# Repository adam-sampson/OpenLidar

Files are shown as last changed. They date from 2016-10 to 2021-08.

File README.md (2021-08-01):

# OpenLidar
Open Lidar

The idea of this project is to use cheap laser distance modules to create 3D scans of the room. This can be done by rotating the laser distance module on 2 axis with the sensor centered on the junction of those two axis (aka: the sensor is on the center of rotation so it's always at the origin). The main goals of this project are to improve the means that cavers use to survey and map caves as citizen scientists, or to create point-clouds for your own purpose.

The project is developed in 3 parts. 1) The hardware for the gimbal. 2) The software to operate the gimbal. 3) Bluetooth/Serial interface for controlling the device with inputs. 

This is a work in progress and has been submitted to the Hackaday Prize. https://hackaday.io/project/11598-open-lidar

The original project had both hardware and software issues and was scrapped for the newer version located here. For older information you will need to checkout previous commits of this git repository. Issues included: not enough ram on the arduino mini pro to fill an SD card write block (extra SD writes = slow), hardware design of the body created too much friction for fast motor operation, hardware was unstable/wobbly, power supply was exceedingly large to fit in case, hardware was not enclosed in protective enclosure, the yaw motor could turn freely (and be knocked out of position easily), the SF-30B module had excessive noise per reading, etc.

The change in case hardware, microchip used, lidar sensor, and yaw motor assembly all necessitated a full rework of the project here.

The current state of the hardware:
- Yaw axis has been completely redesigned to use 30mm shaft through bearing for greater stability
- Pitch axis has been completely redesigned to use "fieldgoal" design to reduce friction and complexity of shaft
- Case parts have been modeled in Fusion 360 but need to finish printing/testing
- Re-selected new hardware to make use of S42B stepper drivers for simplicity and servo-like capabilities

The current status of the software is that it is capable of:
- Capturing data from LidarLitev3 using enhanced library for speeds of up to 2000/s (with ideal I2C conditions)
- Controlling 2 stepper motors 
- Receiving commands and outputing results over serial
- Write to SD card

Future items needed
- Scan Mode to prevent scanRoom from over-sampling near polar regions
- Add ability to read/write settings to ROM
- Add ability to change default settings
- Create progress indicators and time estimates
- Add ability to save as E57 point cloud file
- Add ability to save as xyz point cloud file
- Add routine for identifying 0 degrees
- Add ability to create custom filename (i.e. date and time)

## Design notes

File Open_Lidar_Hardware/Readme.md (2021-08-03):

# Open Lidar Hardware

This section contains the hardware files for the Open Lidar project.

Fusion 360 files are provided as .f3d files. 

Print ready files are provided as .stl files. 

# 3D Printed Case

- LidarLite mount (printed and fitted)
- Gimbal Mount
  - Fieldgoal (printed and fitted)
  - Shaft left/right to act as yaw shaft and mount to field goal (adjusted for better fit)
  - Shaft gear
  - Yaw Motor Gear
  - Slip Ring Connector
  - Body Top
  - Body Middle
  - Body Base
  - Bearing Retention ring

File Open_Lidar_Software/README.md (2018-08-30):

# OpenLidar
Open Lidar

The idea of this project is to use cheap laser distance modules to create 3D scans of the room. This can be done by rotating the laser distance module on 2 axis with the sensor centered on the junction of those two axis (aka: the sensor is on the center of rotation so it's always at the origin). The main goals of this project are to improve the means that cavers use to survey and map caves as citizen scientists, or to create point-clouds for your own purpose.

The current status of the software is that it is capable of:
- Controlling 2 stepper motors (upgraded since last model)
- Receiving commands and outputing results over serial
- Receiving a few commands from a computer/phone over bluetooth
- Creating a unique file name on the SD card

Bluetooth commands:
- cancel;
- pitch turn <float>;
- pitch rpm <int>;
- pitch microstep <int>;
- pitch enable;
- pitch disable;
- yaw turn <float>;
- yaw rpm <int>;
- yaw microstep <int>;
- yaw enable;
- yaw disable;
- yaw max <int>;
- lidar dist;
- lidar scan;
- lidar test;
- bluetooth; (not used yet)
- sd test <string>;
- motor enable;
- motor disable;

Future items needed
- Interfacing over bluetooth
- Reading data from the Lidar Lite V3 module
- Writing to a microSD card
- Create a new scan room function
- Add filter to prevent scanRoom from over-sampling near polar regions
- Add ability to read/write settings to ROM
- Add ability to change default settings
- Create progress indicators and time estimates
- Add ability to save as E57 point cloud file
- Add routine for identifying 0 degrees
- Add ability to create custom filename (i.e. date and time)

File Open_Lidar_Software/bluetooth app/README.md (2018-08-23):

# Bluetooth App

The attached zip file contains an app from http://www.jnhuamao.cn/index_en.asp?ID=1 that allows for connecting to an HM-10 device in windows 10 64 bit. 

This app is required because the BLE device does not get it's own port assigned to it as other non-BLE modules do. 

To install the app follow the instructions in the README inside the zip file. Then find it in your program files just like any other app.

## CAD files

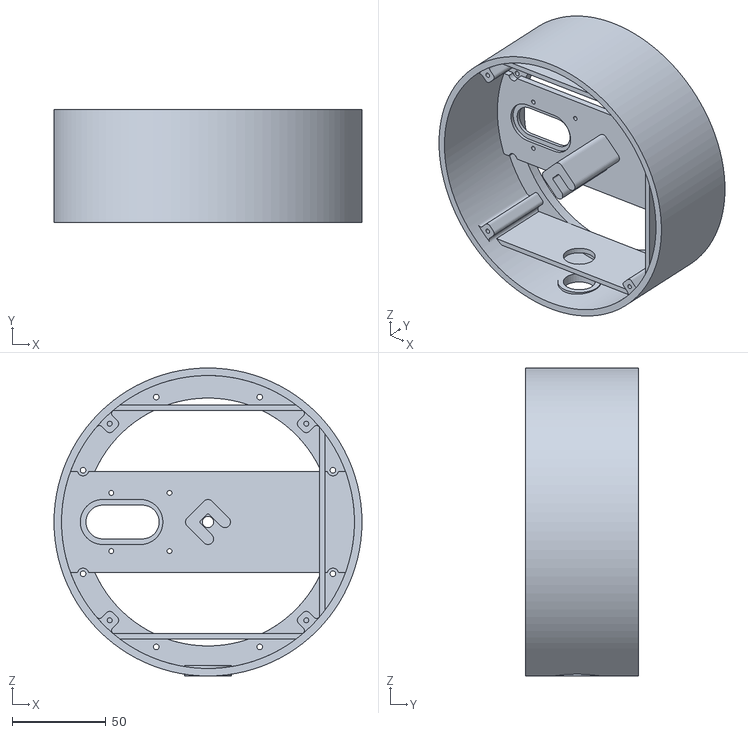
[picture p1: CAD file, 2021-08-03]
Open_Lidar_Hardware/stl/GimbalBaseMiddle.stl
164.0 x 60.0 x 164.0

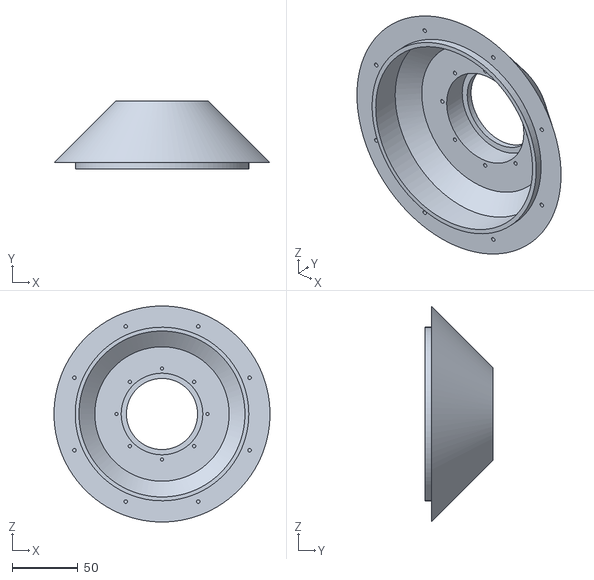
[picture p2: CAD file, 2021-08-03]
Open_Lidar_Hardware/stl/GimbalBaseTop.stl
164.0 x 52.0 x 164.0

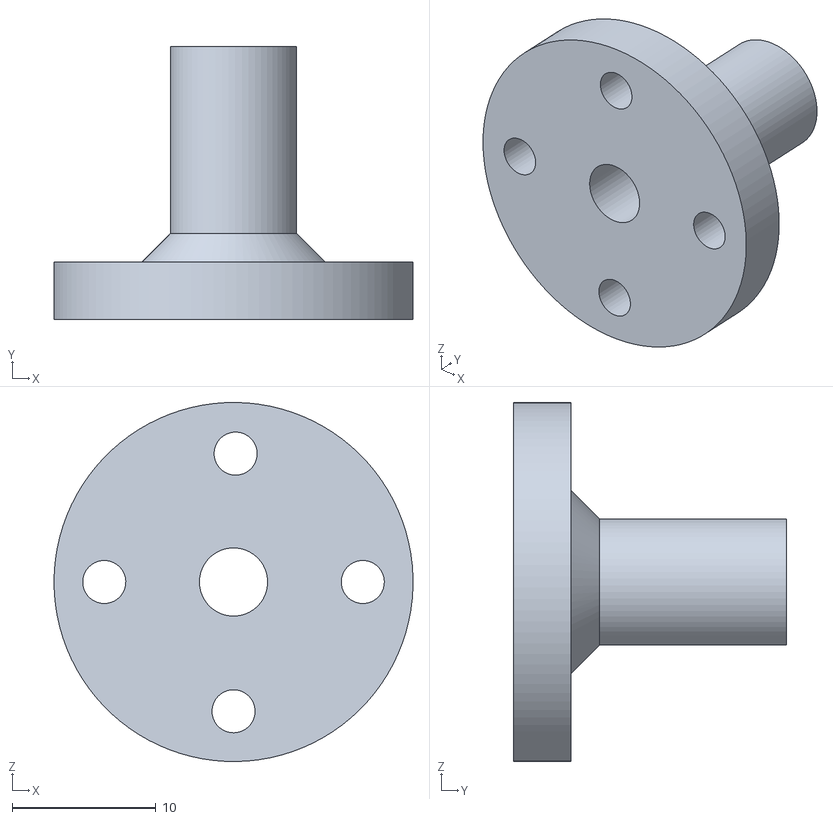
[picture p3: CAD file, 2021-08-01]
Open_Lidar_Hardware/stl/GimbalSlipRingConnector.stl
25.0 x 19.0 x 25.0

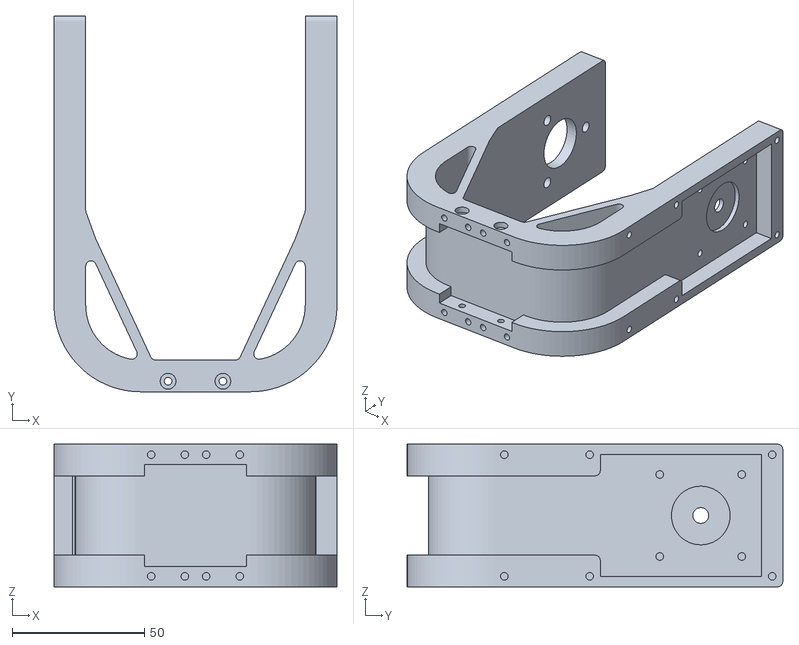
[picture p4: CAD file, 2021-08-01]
Open_Lidar_Hardware/stl/GimalFieldgoal.stl
107.0 x 142.0 x 54.0

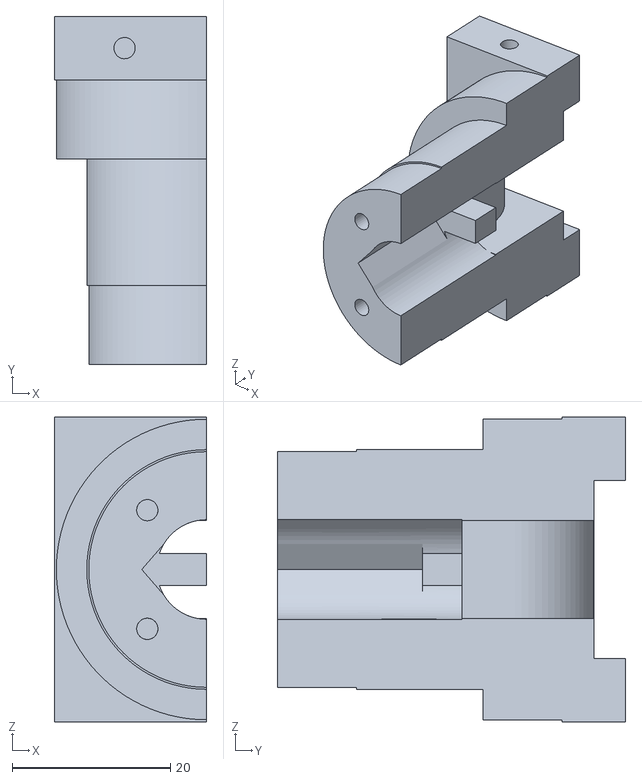
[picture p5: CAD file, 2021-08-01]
Open_Lidar_Hardware/stl/GimbalShaftLeft.stl
19.3 x 44.0 x 38.5

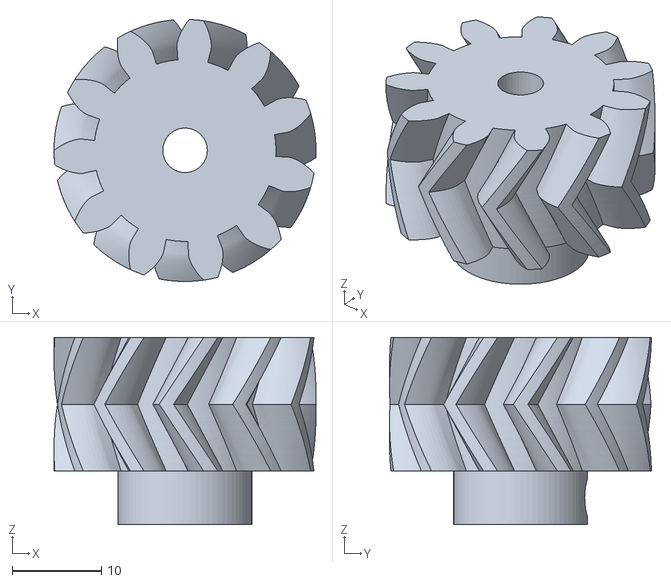
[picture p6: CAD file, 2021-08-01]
Open_Lidar_Hardware/stl/GimbalYawMotorGear.stl
29.4 x 29.4 x 21.0

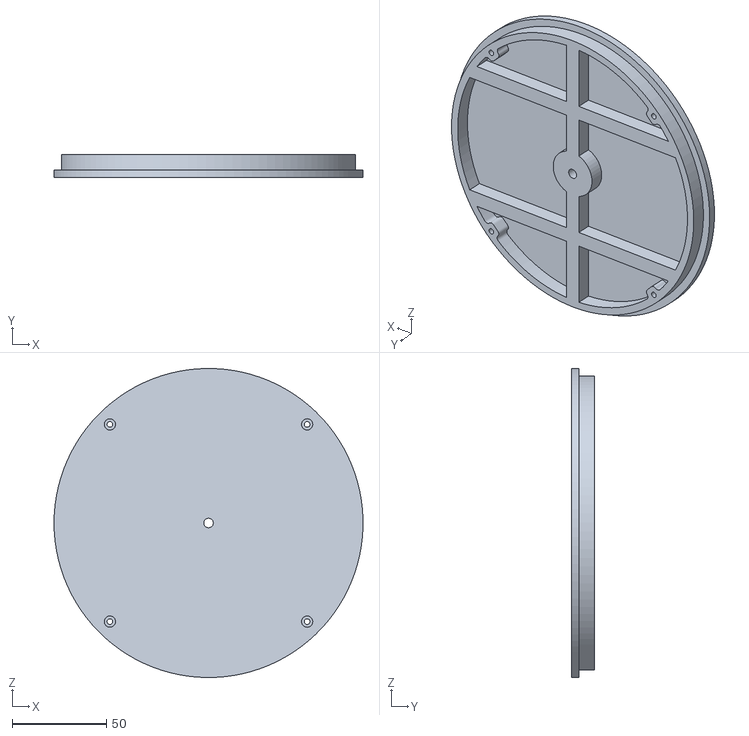
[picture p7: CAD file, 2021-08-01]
Open_Lidar_Hardware/stl/GimbalBaseBottom.stl
164.0 x 12.0 x 164.0

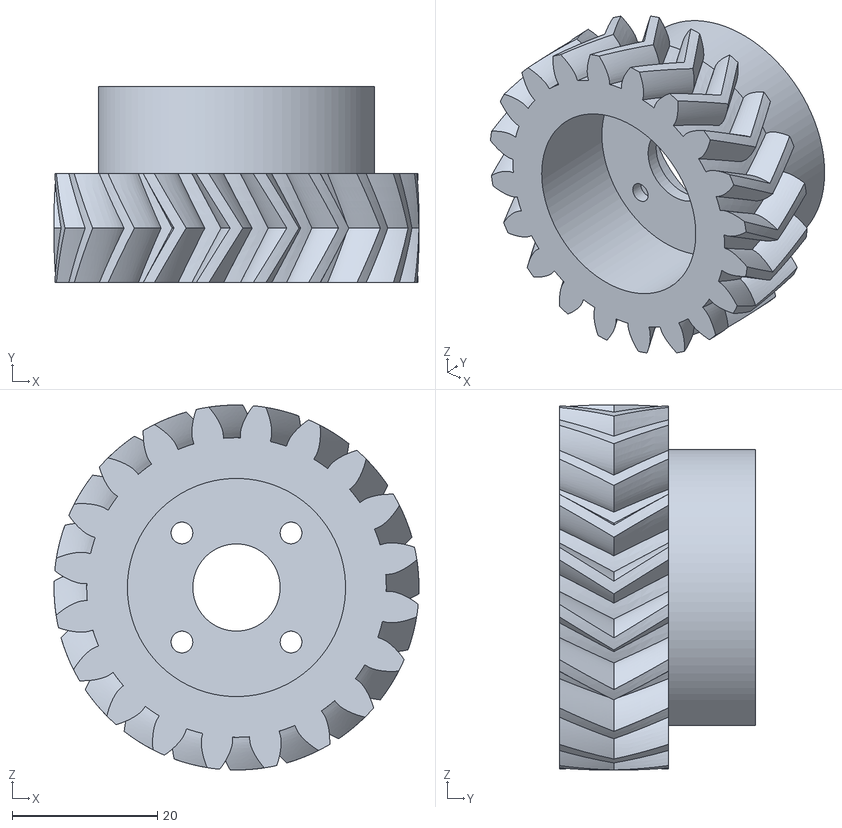
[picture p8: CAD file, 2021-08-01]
Open_Lidar_Hardware/stl/GimbalShaftGear.stl
50.2 x 27.0 x 50.2

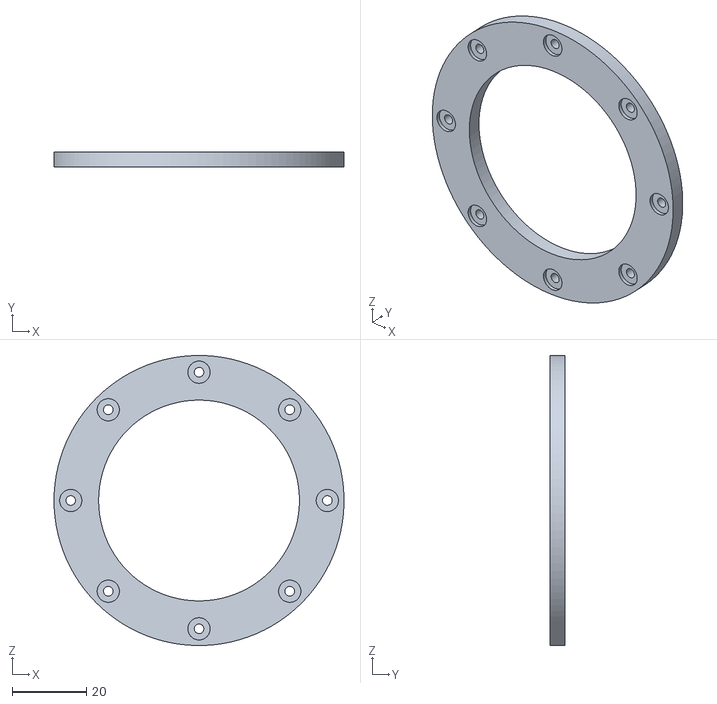
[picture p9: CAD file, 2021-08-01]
Open_Lidar_Hardware/stl/GimbalBearingRetentionRing.stl
78.0 x 4.00 x 78.0

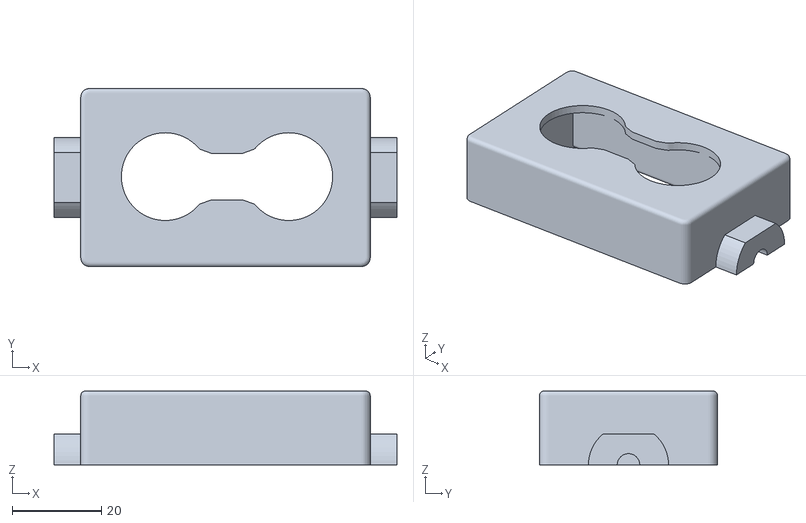
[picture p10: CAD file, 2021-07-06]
Open_Lidar_Hardware/stl/LidarLiteMountFront.stl
77.0 x 40.0 x 16.6

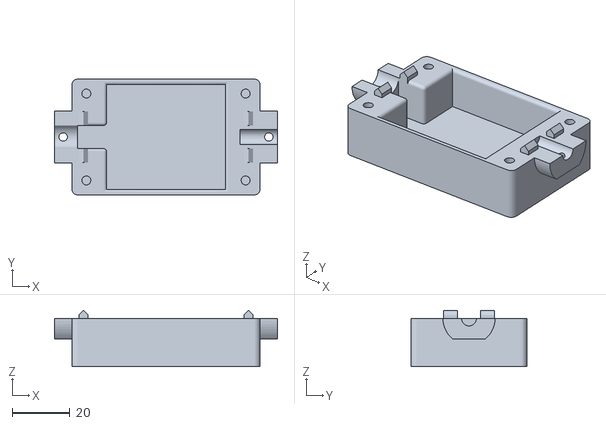
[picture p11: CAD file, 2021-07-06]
Open_Lidar_Hardware/stl/LidarLiteMountBack.stl
77.0 x 40.0 x 19.4

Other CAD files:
Open_Lidar_Hardware/stl/GimbalShaftRight.stl
Open_Lidar_Hardware/OpenLidarGimbal.f3d
Open_Lidar_Hardware/OpenLidarLiteMount.f3d

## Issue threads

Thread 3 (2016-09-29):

scanRoom() over-samples polar regions

caveradam, 2016-09-29:
Because the gimbal only turns on two axis', the polar regions are sampled much more closely than the equatorial regions. For example: Every turn of the pitch motor it points straight up and captures the exact same point (180 times during a scan) but only one scan of the point straight up is required.

This needs to be fixed by decreasing the number of samples taken in equatorial region. For full-step mode (0.9 degrees per step) this fix should yield 36% less data points.

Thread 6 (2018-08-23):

Main body circuit board hole placement

adam-sampson, 2018-08-23:
The standoff/hole to attach the lower-right hole of the circuit board is too close to the yaw motor base. Need to cut away material from stand-off.

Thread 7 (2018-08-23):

Through holes for screws/slipring too tight

adam-sampson, 2018-08-23:
The through holes for screws to pass through are too tight of tolerance. Need to be drilled currently. Same problem for the slipring. Do NOT need to change for hot pressed brass fittings.

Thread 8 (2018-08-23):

SD card not accessible

adam-sampson, 2018-08-23:
The SD card on the teensy is hard to remove because it is inside the case. Need an SD connector/port in the battery box for easy access.

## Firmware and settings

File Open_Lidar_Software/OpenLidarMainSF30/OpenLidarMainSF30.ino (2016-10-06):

/*     Open Lidar Project Code
 *     Author: Adam Sampson
 *     
 *     License: The software in this project is licensed under the GPLv3 lisence. The 
 *     hardware is licensed under the TARP Open Hardware License v1.0. 
 *     
 *     Acknowledgements - This project uses commonly available tutorials and libraries. 
 *     The code has been modified to meet the needs of the project. This project has been 
 *     made possible by the generous work of everyone in the open source community. As such
 *     it is only fair to make this project open source.
 *     
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
 *     SD card attached to the SPI BUss
 *     ** NOTE: This REQUIRES >100 mA of current. This cannot run off the trinket pro 5V pin.
 *       MOSI - Pin 11
 *       MISO - Pin 12
 *       CLK - Pin 13
 *       CS - Pin 10
 *     
 *     Bluetooth Connected to the TX/RX pins
 *       TX - Pin 1 on Arduino to RX on Bluetooth Module
 *       RX - Pin 0 on Artuino to TX on Bluetooth Module
 *       Question: Is there a 20byte transmit limit?
 *     
 *     Hall Effect digital out connected to the A0 pin
 *       D0 - Pin A2
 *     
 *     Motor Common Pin
 *      SLP/RST - Pin 8 //High to enable A4988 board, Low to sleep
 *      MS1 - Pin 9
 *      MS2 - Pin A3
 *          **************************
 *          *              MS1   MS2 * 
 *          *Full Step     Low   Low *
 *          *Half Step     High  Low *
 *          *Quarter Step  Low   High*
 *          *Eighth Step   High  High*
 *          **************************
 *     
 *     Motor 1 (pitch) connected to digital output pins
 *       Step - Pin 4
 *       Direction - Pin 3
 *     
 *     Motor 2 (yaw) connected to digital output pins
 *       Step - Pin 6
 *       Direction - Pin 5
 *     
 *     SF30-B connected to digital input/output pins through SoftwareSerial
 *       Rx Arduino - TXD SF30 (yellow) - Pin A0 as INPUT
 *       Tx Arduino - RXD SF30 (orange) - Pin A1 as OUTPUT
 */

#include <SPI.h>
#include <SD.h>
#include <SoftwareSerial.h>
#include <MemoryFree.h>

#define DEBUG

#ifdef DEBUG
 #define DEBUG_PRINTLN(x)  Serial.println (x)
 #define DEBUG_PRINT(x) Serial.print (x)
#else
 #define DEBUG_PRINT(x)
 #define DEBUG_PRINTLN(x)
#endif

#define TerminalBAUD 9600  //38400    //Baud rate of serial or bluetooth output
#define serial_Rxd A0         //Pin definitions to match wiring to SF30
#define serial_Txd A1
#define sf30BAUD 38400        //SF30 baud rate

SoftwareSerial sf30_serial(serial_Rxd, serial_Txd);

// define variables to read into from SF30 laser distance
float sfDistance;
int Byte_L, Byte_H;

// define an array of characters to read serial into for bluetooth commands
String serialData;

// define pins numbers
const int PROGMEM slpPin = 8;
const int PROGMEM MS1Pin = 9;
const int PROGMEM MS2Pin = A3;

const int PROGMEM stepPin1 = 4; // motor 1 step pin
const int PROGMEM dirPin1 = 3;  // motor 1 direction pin
const int PROGMEM stepPin2 = 6; // motor 2 step pin 
const int PROGMEM dirPin2 = 5;  // motor 2 direction pin
const int PROGMEM digHall = A2; // digital hall effect pin

// define motor profile
const int PROGMEM riseDelay1 = 2;
const int PROGMEM fallDelay1 = 2;
const int PROGMEM riseDelay2 = 2; 
const int PROGMEM fallDelay2 = 2;
const unsigned long PROGMEM pitchMotDelay = 350;
const unsigned long PROGMEM yawMotDelay = 2400; 
unsigned long  pitchMotMicroCounter; 
unsigned long yawMotMicroCounter; 

int myYawSteps = 400*2;  // This is a 400 step motor with Eighth Steps and yaw only goes half around
int myPitchSteps = 400*4;  // This is a 400 step motor with Eight Steps

// define SD card variables
File myFile;
//boolean mySdStatus = 0;
const int PROGMEM slaveSelect = 10; // Pin 10 is the chip select pin
const int PROGMEM readingsPerWrite = 320;

/*
* Setup Function - Run once
*/
void setup() {
  // put your setup code here, to run once:
  // Set serial for bluetooth (or FTDI)
  Serial.begin(TerminalBAUD);
  //while (!Serial);  //Wait for serial before doing anything else

  //Setup the SF30
  sf30_serial.begin(sf30BAUD);
  //By Default we turn off the SF30 so it isn't running while we are in standby
  sf30_serial.print("#N");
  //DEBUG_PRINTLN("Turned off SF30");
  sf30_serial.print(F("#R3:"));  //Set the measurement resolution to 0.03m NOT smoothed
  sf30_serial.print(F("#U1665:"));  //Set the measurement rate to 1665 per second
  sf30_serial.print(F("#p0:"));  //Set the output to distance in meters.
  //DEBUG_PRINT("SF set to 0.03m ");
  //DEBUG_PRINT("resol. (unsmooth) ");
  //DEBUG_PRINTLN("1665 times/second");

  // Set motors to sleep mode to conserve power
  pinMode(slpPin,OUTPUT);
  digitalWrite(slpPin,LOW);

  // Set motor delay variables
  pitchMotMicroCounter = micros();
  yawMotMicroCounter = micros (); 

  // Set common motor pins to default Eighth Step Mode 
  pinMode(MS1Pin,OUTPUT);
  pinMode(MS2Pin,OUTPUT);
  digitalWrite(MS1Pin,HIGH);
  digitalWrite(MS2Pin,HIGH);
  
  // Sets the motor driver pins as Outputs
  pinMode(dirPin1,OUTPUT);
  pinMode(stepPin1,OUTPUT); 
  pinMode(dirPin2,OUTPUT);
  pinMode(stepPin2,OUTPUT); 

  // Sets the Hall Effect pin as Input
  pinMode(digHall,INPUT);

 
  // Set up the SD card
  pinMode(slaveSelect,OUTPUT); //attempting to prevent hardware from setting Arduino as Slave
  //DEBUG_PRINTLN(F("Initilazing SD card..."));
  if (!SD.begin(slaveSelect)) {
    DEBUG_PRINTLN(F("SD Init Failed."));
    //mySdStatus = 0;
  }
  else {
    DEBUG_PRINTLN(F("SD Init. Complete."));
    //mySdStatus = 1; 
  }
  /*
  if (mySdStatus == 1) {
    if (SD.exists("DEBUG.txt")) {
      DEBUG_PRINTLN("DEBUG.txt exists. Able to read/write SD card.");
      delay(100); //let bluetooth catch up
      DEBUG_PRINTLN("Deleting file.");
      SD.remove("DEBUG.txt");
      if (SD.exists("DEBUG.txt")) {
        DEBUG_PRINTLN("Delete failed.");
      }
      else {
        DEBUG_PRINTLN("Delete succeeded.");
      }
      
    }
  else {
      //DEBUG_PRINTLN("Creating fresh DEBUG.txt");
      myFile = SD.open("DEBUG.txt", FILE_WRITE);
      myFile.close();
  
      if (SD.exists("DEBUG.txt")) {
        //DEBUG_PRINTLN("DEBUG.txt created. Able to read/write SD card.");
        delay(1); //let bluetooth catch up
      }
    }
  }
  */
  /*
  if (SD.exists(F("DEBUG.txt"))) {  //if the file doesn't exist, return the name
      DEBUG_PRINTLN(F("Found Debug.txt"));
      delay(100);
    }
  */
  DEBUG_PRINTLN(F("Setup complete"));
}

/*
* Loop Function - Run forever
*/
void loop() {
  // Set variables
  unsigned long microcounter;
  microcounter = micros();
  String testFilename;

  //delay(10000); // 10 second delay to get hands out of the way

  //Listen for bluetooth commands
  while(Serial.available()) {
    serialData = Serial.readString(); //read incoming data as a string
    //DEBUG_PRINT("OL recieved: ");
    DEBUG_PRINTLN(serialData);
  }

  //Decide what to do with the command recieved
  if(serialData.startsWith(F("TestMotors"))) {
    for (int j = 0; j < 1; j++) {  //test the motor j times.
    // Make sure they aren't sleeping
    digitalWrite(slpPin,HIGH);
    delay(500);
    // Test motor 1 for 20 steps at default quarter step of 0.9deg
    TestMotor(1,myPitchSteps);
    delay(500);
    //Test motor 2 for 20 steps at default quarter step of 0.9deg
    TestMotor(2,myYawSteps);
    delay(500);
    }

    // Put the motor to sleep to save power
    digitalWrite(slpPin,LOW);

    //Unset the command string so we don't repeat next loop
    serialData = "";
  }
  else if (serialData.startsWith(F("ScanRoom"))) {
    delay(1);
    scanRoom(); 
    //Unset the command string so we don't repeat next loop
    serialData = ""; 
  }
  else if (serialData.startsWith(F("TestSF30"))) {
    TestSF30();
    //Unset the command string so we don't repeat next loop
    serialData = "";
  }
  else if (serialData.startsWith(F("TestSD"))) {
    if (SD.exists("DEBUG.txt")) {  //if the file doesn't exist, return the name
      DEBUG_PRINTLN(F("Found DEBUG.txt"));
      delay(100);
    }
    testFilename = createNewFileName();
    DEBUG_PRINT(F("Created file: "));
    DEBUG_PRINTLN(testFilename);
    serialData = "";
  }
}

/*
* readHall function - return 0 or 1 depending on magnet presence
*/
boolean readHall() {
  boolean digHallState = 0;
  return digitalRead(digHall);
  //DEBUG_PRINT("Digital Hall State: ");
  //DEBUG_PRINTLN(digHallState);
}

/*
* StepMotorForward function - move selected motor forward 1 step
* Currently allows motor 1 or motor 2 as inputs only. 
* Motor movement delay is coded through micro counter
*/
void StepMotorForward(int Motor){
  //temp variables
  int tempStepPin;
  int tempDirPin;

  switch(Motor) {
    case 1:
      while (micros() - pitchMotMicroCounter < pitchMotDelay) {
        //wait until enough time has passed before trying to move the motor again without using delay
      }
      tempStepPin = stepPin1;
      tempDirPin = dirPin1;
      digitalWrite(tempDirPin,HIGH);
      digitalWrite(tempStepPin,HIGH);
      delayMicroseconds(riseDelay1);
      digitalWrite(tempStepPin,LOW);
      delayMicroseconds(fallDelay1);
      //reset the counter to new time
      pitchMotMicroCounter = micros();
      break;
    case 2:
      while (micros() - yawMotMicroCounter < yawMotDelay) {
        //wait until enough time has passed before trying to move the motor again without using delay
      }
      tempStepPin = stepPin2;
      tempDirPin = dirPin2;
      digitalWrite(tempDirPin,HIGH);
      digitalWrite(tempStepPin,HIGH);
      delayMicroseconds(riseDelay2);
      digitalWrite(tempStepPin,LOW);
      delayMicroseconds(fallDelay2);
      //reset the counter to new time
      yawMotMicroCounter = micros();
      break;
    default: //we only have two motors...cancel if something else selected
      return;
      break;
  }
  
  
/*
* TestMotor function - basic test that motors are working
*/
}

void TestMotor(int Motor, int Steps) {
  //Make sure the motors are not sleeping
  digitalWrite(slpPin,HIGH);

  //
  for (int i=0; i <= Steps; i++) {
    StepMotorForward(Motor);
  }
}

/*
* TestWriteToSD function - debugging purposes to see if SD works
*/
/*
void TestWriteToSD() {
  //DEBUG_PRINT("SD Status: ");
  //DEBUG_PRINT(mySdStatus);
  //DEBUG_PRINT("  ");
  
  // re-open the file for writing
  myFile = SD.open("DEBUG.txt", FILE_WRITE);

  // if the file opened okay, write to it
  if (myFile) {
    //DEBUG_PRINTLN("Printing to file");
    myFile.println(F("File Found"));
    //myFile.println(mySdStatus);
    myFile.close(); // Make sure to close the file to save changes.
  }
  else {
    DEBUG_PRINTLN(F("Error test SD"));
  }
  DEBUG_PRINTLN(F("SD pass"));
}
*/

/*
* TestSF30 Function - See if we can read from the SF30 sensor
* Read the sensor 10 times and report over serial debug
*/
void TestSF30() {
  int isSfData = 0; 

  // Start the SF30
  sf30_serial.print("#Y");
  //DEBUG_PRINTLN("Turned on SF30");
  
  //clear the buffer to avoid earlier readings
  while (sf30_serial.available() > 0) {
    Byte_H = sf30_serial.read();
    while (!sf30_serial.available()); //Don't get off order, wait for second bit.
    Byte_L = sf30_serial.read();
    //do nothing with this data, but throw it away as old data
  }
  //DEBUG_PRINTLN("Cleared old data");
  delayMicroseconds(500);

  //DEBUG_PRINTLN("Beginning SF30 Reading");
  delay(1); //let bluetooth catch up
  sf30_serial.available();
  for(int tt = 0; tt < 10; tt++) {
    if (sf30_serial.available() > 0) {
      while (!sf30_serial.available());
      Byte_H = sf30_serial.read();
      while (!sf30_serial.available()); //Don't get off order, wait for second bit.
      Byte_L = sf30_serial.read();
      sfDistance = (float(Byte_L))/256 + Byte_H;
      DEBUG_PRINT(F("Distance in meters = "));
      DEBUG_PRINTLN(sfDistance);
      isSfData += 1; 
    }
    delayMicroseconds(500); //delay 700us before next reading
  }
  if (isSfData == 0) {
    DEBUG_PRINTLN(F("No data collected from SF30"));
    delay(1); //let bluetooth catch up
  }
  sf30_serial.print("#N");
  //DEBUG_PRINT("Turned off SF30");
}

/*
* warmupSF30 function - warm up the sensor to get more precise readings
* run 30 seconds to warm up
*/
void warmupSF30 () {
  //Warm up the sensor by running it for 30 seconds.
  unsigned long warmupCounter;
  
  // Start the SF30
  sf30_serial.print("#Y");
  warmupCounter = millis();
  DEBUG_PRINTLN(F("Start Warmup"));

  //DEBUG_PRINTLN("Begin SF30 Reading");
  sf30_serial.available();
  while (millis() - warmupCounter < 10000) {
    if (sf30_serial.available() > 0) {
      while (!sf30_serial.available());
      Byte_H = sf30_serial.read();
      while (!sf30_serial.available()); //Don't get off order, wait for second bit.
      Byte_L = sf30_serial.read();
      sfDistance = (float(Byte_L))/256 + Byte_H;
      //DEBUG_PRINT("Distance in meters = ");
      //DEBUG_PRINTLN(sfDistance); 
    }
  }

  sf30_serial.print("#N");
  delay(100);
  //DEBUG_PRINTLN("Turned off SF30");
  
  DEBUG_PRINTLN(F("Warmed up"));
  delay(100); //let serial catch up
}

/*----------------------------------------------------------------
* scanRoom function - what we've been waiting for...actually scan the room
*/
void scanRoom() {
  DEBUG_PRINTLN(F("Start room scan"));
  
  //Define Variables
  float range,azimuth,polar;
  float degPerYawStep = float(360)/myYawSteps;
  float degPerPitchStep = float(360)/myPitchSteps;
  unsigned long shotCounter = 0;
  unsigned int bufferCounter = 0;

  char readingBuffer [9]; //Need 8 + 1 for trailing null from dtostrf
  char sdBuffer [512];  //Need to send 512 bytes per block to SD card

  //test varialbes to delete later
  float testrange = 39.999;
  float testazimuth = 99.9999;
  float testpolar = 100.99;
  float testintensity = 256.0;

  //Warmup the SF30
  warmupSF30();

  //Make sure the motors are not sleeping
  digitalWrite(slpPin,HIGH);

  //Open the SD card
  DEBUG_PRINTLN(F("Start SD card"));
  delay(10);

  if (SD.exists("OL1.CSV")) {
   //DEBUG_PRINTLN("Can access SD card, but can't open new file");
   //delay(1); //let bluetooth catch up
   SD.remove("OL1.CSV");
  }

  delay(100);

  myFile = SD.open("OL1.CSV", FILE_WRITE);
  myFile.println("Range,Azimuth,Polar");
  myFile.close();

  //test the file for debug purposes
  delay(100);
  myFile = SD.open("OL1.CSV"); //Open for reading
  if(myFile) {
    Serial.println(F("OL1.CSV opened"));
    while (myFile.available()) {
      Serial.write(myFile.read());
    }
    myFile.close();
  }
  else {
    Serial.println(F("Error opening OL1.SCV"));
  }

  //Begin scanning procedure
  //Turn the pitch motor 1 full turn while taking measurements
  //Write to SD card every 512 Bytes
  //Turn azimuth motor 1 'step' for each pitch motor turn
  
  //Turn on the SF30
  sf30_serial.print("#Y");
  delay(10);
  
  myFile = SD.open("OL1.CSV", FILE_WRITE);
  //myFile.println("Range,Azimuth,Polar,Intensity");
  //myFile.close();
  DEBUG_PRINTLN(F("Scanning"));
  delay(100); //let bluetooth catch up
  
  //Turn Azimuth
  //for(int aloop = 0; aloop < myYawSteps; aloop++) {
  for(int aloop = 0; aloop < myYawSteps; aloop++) {
    // Calculate the azimuth for this loop
    azimuth = float(aloop)*degPerYawStep;

    //Turn Pitch
    for(int ploop = 0; ploop < myPitchSteps; ploop++) {
    //for(int ploop = 0; ploop < 16; ploop++) {
      // Take a measurement
      //If there are more than 1 reading (2 bytes) then we have gotten ahead of ourselves
      while (sf30_serial.available() > 2) { //If there are more than 1 measurement to be read
        Byte_H = sf30_serial.read();
        while (!sf30_serial.available()); //Don't get off order, wait for second bit.
        Byte_L = sf30_serial.read();
        //do nothing with this data, but throw it away as old data
      }
      
      while (!sf30_serial.available());
      Byte_H = sf30_serial.read();
      while (!sf30_serial.available()); //Don't get off order, wait for second bit.
      Byte_L = sf30_serial.read();
      range = (float(Byte_L))/256 + Byte_H;
      polar = float(ploop)*degPerPitchStep;

      //add readings to sdBuffer in 32 byte increments
      //8 range 1 ',' 8 azimuth 1 ',' 8 polar 1 ',' 3 intensity 1 'lf' 1'cr'
      dtostrf(range,8,4,readingBuffer);
      //dtostrf(testrange,8,4,readingBuffer);
      //DEBUG_PRINT(freeMemory());
      //DEBUG_PRINT("    ");
      //DEBUG_PRINT(shotCounter%16);
      //DEBUG_PRINT("    ");
      //delay(100);
      for (int br= 0; br < 8; br++) {
        sdBuffer[(32*(shotCounter % 16)+br)] = readingBuffer[br];
      }
      sdBuffer[(32*(shotCounter%16)+8)] = ',';
      dtostrf(azimuth,8,4,readingBuffer);
      //dtostrf(testazimuth,8,4,readingBuffer);
      for (int ba= 0; ba < 8; ba++) {
        sdBuffer[(32*(shotCounter % 16)+9+ba)] = readingBuffer[ba];
      }
      sdBuffer[(32*(shotCounter%16)+17)] = ',';
      dtostrf(polar,8,4,readingBuffer);
      //dtostrf(testpolar,8,4,readingBuffer);
      for (int bp= 0; bp < 8; bp++) {
        sdBuffer[(32*(shotCounter % 16)+18+bp)] = readingBuffer[bp];
      }
      sdBuffer[(32*(shotCounter%16)+26)] = ',';
      dtostrf(testintensity,5,0,readingBuffer);
      for (int bi= 0; bi < 3; bi++) {
        sdBuffer[(32*(shotCounter % 16)+27+bi)] = readingBuffer[bi+2];
      }
      sdBuffer[(32*(shotCounter % 16)+30)] = ' ';
      sdBuffer[(32*(shotCounter % 16)+31)] = 10;
      

      //If we are at the end of the buffer shotcounter % 16 = 15
      //Send the buffer to the sd card
      if (shotCounter % 16 == 15) {
        //DEBUG_PRINTLN("Write Loop");
        //delay(100);
        myFile.write(sdBuffer,512);
      }

      //Step the pitch motor forward 1 step
      //For now, run forward 2 eighth steps to get quarter step...need improvement
      StepMotorForward(1);
      StepMotorForward(1);

      //Increment the shot counter every time we take a shot
      shotCounter += 1;
    } //end pitch loop

    //DEBUG_PRINTLN("Yaw Loop");
    //Once every yaw cycle save the file in case of crash
    myFile.flush();

    // Check for a cancel command
    while(Serial.available()) {
    serialData = Serial.readString(); //read incoming data as a string
      if(serialData.startsWith(F("Cancel"))) {
        DEBUG_PRINTLN(F("Cancel received."));
        //Close the file
        myFile.close();
        //Put the SF30 back to sleep to save power
        sf30_serial.print("#N");
        delay(10);
        //Turn off the motors
        digitalWrite(slpPin,LOW);
        return;
      }
    }

    // Run the Yaw motor forward 1 step since the pitch has run a full rotation
    //For now, run forward 2 eighth steps to get quarter step...need improvement
    StepMotorForward(2);
    StepMotorForward(2);
    
  }  //end azimuth loop

  //Make sure the motors are sleeping
  digitalWrite(slpPin,LOW);
  //myFile.println("Testafterloop");
  myFile.close();
  //test the file for debug purposes
  delay(100);
  /*
  myFile = SD.open("OL1.CSV"); //Open for reading
  if(myFile) {
    Serial.println(F("OL1.CSV opened"));
    while (myFile.available()) {
      Serial.write(myFile.read());
    }
    myFile.close();
  }
  else {
    Serial.println(F("Error opening OL1.SCV"));
  }
  */
  DEBUG_PRINTLN("Scan Complete");
}
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

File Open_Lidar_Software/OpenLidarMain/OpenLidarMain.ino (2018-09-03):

/*     Open Lidar Project Code
 *     Author: Adam Sampson
 *     
 *     License: The software in this project is licensed under the GPLv3 lisence. The 
 *     hardware is licensed under the TARP Open Hardware License v1.0. 
 *     
 *     Acknowledgements - This project uses commonly available tutorials and libraries. 
 *     The code has been modified to meet the needs of the project. This project has been 
 *     made possible by the generous work of everyone in the open source community. As such
 *     it is only fair to make this project open source.
 *     
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
 *     Bluetooth Connected to the TX/RX pins
 *       TX - Pin TX5 on Arduino to RX on Bluetooth Module
 *       RX - Pin RX5 on Artuino to TX on Bluetooth Module
 *       Use Serial5.function to control this.
 *     
 *     Motor Details
 *          **************************
 *          *              Mode0 Mode1 Mode2 * 
 *          *Full Step     Low   Low   Low   *
 *          *1/2 Step      High  Low   Low   *
 *          *1/4 Step      Low   High  Low   *
 *          *1/8 Step      High  High  Low   *
 *          *1/16 Step     Low   Low   High  *
 *          *1/32 Step     High  High  High  *
 *          **************************
 *     
 *     Motor 1A (pitch) connected to digital output pins
 *       EN  - 2
 *       M0  - 3
 *       M1  - 4
 *       M2  - 5
 *       RST - 6
 *       SLP - 7
 *       STP - 8
 *       DIR - 9
 *     
 *     Motor 0.6A (yaw) connected to digital output pins
 *       EN  - 12
 *       M0  - 24
 *       M1  - 25
 *       M2  - 26
 *       RST - 27
 *       SLP - 28
 *       STP - 29
 *       DIR - 30
 *       
 *     Lidar Lite V3 connected to I2C pins
 *       SCL0 - digital pin 19
 *       SDA0 - digital pin 18
 *
 * Warning SdFatSdio and SdFatSdioEX normally should 
 * not both be used in a program.
 * Each has its own cache and member variables.
 * 
  */

// Define Libraries
#include <DRV8825.h>          // Pololu motor driver library
#include <i2c_t3.h>           // Wire.h functions for the 32 bit teensy 3.5
#include <I2CFunctions.h>     // EnhancedLidar library
#include <LidarObject.h>      // EnhancedLidar library
#include <LidarController.h>  // EnhancedLidar library
#include "SdFat.h"            // SD card library

// Define whether or not to use DEBUG mode
#define DEBUG

// Define serial command object
#define mySerial Serial5 // Define to serial you want to use...Serial for usb, Serial5 for bluetooth
const byte numChars = 32;
char receivedChars[numChars];
boolean receiveFull = false;
#define MAX_WORD_COUNT 3
#define MIN_WORD_COUNT 2
char *Words[MAX_WORD_COUNT];
boolean lockSerial = false; // Some functions may want to allow only "Cancel" as a command
boolean cancel = false; // Functions that allow cancel will check for this flag each major loop

#ifdef DEBUG
 #define DEBUG_PRINTLN(x)  mySerial.println (x)
 #define DEBUG_PRINT(x) mySerial.print (x)
#else
 #define DEBUG_PRINT(x) // do nothing
 #define DEBUG_PRINTLN(x) // do nothing
#endif

#define TerminalBAUD 9600  //38400    //Baud rate of serial or bluetooth output

// Define Lidar related variables
#define WIRE400K true
// Trigger pin, can be unplugged
#define Z1_LASER_TRIG 0
// Enable pin, IMPORTANT
#define Z1_LASER_EN 17
// Mode pin, can be unplugged
#define Z1_LASER_PIN 0
//Define address of lasers
//Thoses are written during initialisation
// default address : 0x62
#define Z1_LASER_AD 0x62

#define NUMBER_OF_LASERS 1

#define GIMBAL_OFFSET 2

// Delays
long currMicro, lastMicro;
int shotMicroDelay = 100;
boolean distanceReady = false;
int microCnt;

// Create lasers
static LidarController Controller;
static LidarObject LZ1;

// Define motor structure
typedef struct {
  int EN;
  int M0;
  int M1;
  int M2;
  int RST;
  int SLP;
  int STP;
  int DIR;
  int steps; // Number of steps in a full turn
  int microstep; //Fraction to microstep. I.E. 4 is quarter step.
  int rpm; // Max speed of motor in rotations per minute
}motorStruct;

motorStruct pitch = {2,3,4,5,6,7,8,9,400,32,180};
motorStruct yaw = {12,24,25,26,27,28,29,30,8000,32,10};
float maxYawDeg = 180;

// Initiate the motors using the DRV8825 library
DRV8825 pitchMot(pitch.steps,pitch.DIR,pitch.STP,pitch.EN,pitch.M0,pitch.M1,pitch.M2);
DRV8825 yawMot(yaw.steps,yaw.DIR,yaw.STP,yaw.EN,yaw.M0,yaw.M1,yaw.M2);

// Define variables for writing to the SD Card
//==============================================================================
// Error messages stored in flash.
#define error(msg) sd.errorHalt(F(msg))

// file system
SdFatSdio sd;
SdFile file;

// Log file base name.  Must be six characters or less.
#define FILE_BASE_NAME "OL"
char fileName[10] = FILE_BASE_NAME "000.sph";

// define a struct to hold a lidar reading
typedef struct{
  uint16_t radius;
  float yaw;
  float pitch;
  byte intensity;
}Readings;

Readings reading;

/*
* Setup Function - Run once
*/
void setup() {
  // put your setup code here, to run once:
  
  // Set serial communication for whichever serial port chosen above
  mySerial.begin(TerminalBAUD);

  pitchMot.begin(pitch.rpm);
  yawMot.begin(yaw.rpm);

  // Set the microstep mode
  pitchMot.setMicrostep(pitch.microstep);
  yawMot.setMicrostep(yaw.microstep);
  
  pitchMot.disable(); // No need to use power until command received
  yawMot.disable(); // No need to use power until command received

  pinMode(pitch.SLP, OUTPUT);
  pinMode(pitch.RST, OUTPUT);
  pinMode(yaw.SLP,   OUTPUT);
  pinMode(yaw.RST,   OUTPUT);

  // Disable sleep and set reset. Rely on EN pin to enable or disable stepper.
  digitalWrite(pitch.SLP,LOW);
  digitalWrite(yaw.SLP,  LOW);
  digitalWrite(pitch.RST,LOW);
  digitalWrite(yaw.RST  ,LOW);  

  // Configure lasers
  LZ1.begin(Z1_LASER_EN, Z1_LASER_PIN, Z1_LASER_TRIG, Z1_LASER_AD, 2, DISTANCE, 'A');
  LZ1.setCallbackDistance(&distance_callback);
  // Add the laser to the Controller
  Controller.add(&LZ1, 0);
  
  delay(100);
  Controller.begin(WIRE400K);
  delay(100);

  //setup sd card
  if (!sd.begin()) {
    DEBUG_PRINTLN("Unable to begin SD card. Power off, check SD card, and try again.");
    //sd.initErrorHalt();
  }

  mySerial.println(F("OpenLidar Ready."));
}

/*
* Loop Function - Run forever
*/
void loop() {
  // Set variables

  //delay(5000); // 5 second delay to get hands out of the way
  checkSerial();
  cancel = false; // The loop doesn't care about cancel, so uncheck it
}

// Write data header.
void writeHeader() {
  file.print(F("radius(int),pitch(flt),yaw(flt),intensity(byte)"));
  file.println();
}
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

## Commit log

2016-09-29 Add files via upload
    Full functionality, known error at end of warmup.
    [OpenLidarMain.ino]
2018-05-28 Updating project to v3
    [Assembly1.0001.iam, Assembly1.iam, LidarLiteV3Mount.ipt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]
2018-05-29 Updated models much better design
    [Assembly1.0001.iam, Assembly1.0003.iam, Assembly1.iam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]
2018-05-29 added wire hole to lidar mount
    [LidarLiteV3Mount.0004.ipt, LidarLiteV3Mount.ipt, LidarLiteV3Mount.stl]
2018-05-29 Added circuit board mounting holes to body
    [Main Lidar Body.0014.ipt, Main Lidar Body.0015.ipt, Main Lidar Body.ipt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]
2018-05-29 Added mounting bracket for pitch motor and magnetic encoder.
    [Assembly1.0003.iam, Assembly1.0005.iam, Assembly1.iam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]
2018-05-29 Added lidar housing to assembly.
    [Assembly1.0005.iam, Assembly1.0007.iam, Assembly1.iam]
2018-06-05 Updated models and stl files
    [Assembly1.0007.iam, Assembly1.0008.iam, Assembly1.iam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]
2018-08-06 Repaired Yaw Motor Mount
    Yaw motor mount was mis-measured. New yaw motor mount tilts the motor and places the shaft on the case side of the box.
    [Yaw Motor Mount_v2.0003.ipt, Yaw Motor Mount_v2.ipt, Yaw Motor Mount_v2.stl]
2018-08-18 cleanup hardware model files
    [Yaw Motor Mount.ipt, Yaw Motor Mount_v2.ipt]
2018-08-19 Updating code for new hardware
    [BatteryBox.0002.ipt, BatteryBox.0003.ipt, BatteryBox.ipt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]
2018-08-21 motors and serial working
    Update with motors and serial commands working on new hardware.
2018-08-24 Updating main file to take lidar measurements
2018-08-28 Added simple lidar scan code
2018-08-28 fixes to motor in scan
    [OpenLidarMain.ino]
2018-08-30 Fixed initial setting of microstep mode
    [OpenLidarMain.ino]
2018-09-03 remove arduino cli file
2021-07-06 Add files via upload
    Field goal, lidar mount front/back.
    [LidarLiteMountFront.stl, LidarliteFieldgoal.stl, LidarliteMountBack.stl]
2021-08-01 Updated to Current Summer 2021 status
    Updated to Current Summer 2021 status
    [Assembly1.0008.iam, Assembly1.iam, BatteryBox.0003.ipt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]
2021-08-03 Removed offset face from bearing fit
    Bearing press fit holds in place but could use a tighter press fit. Removed 0.1mm offset face to create tighter press fit.
    [GimbalBaseTop.stl, OpenLidarGimbal.f3d]
2021-08-03 Added Flat for Cable Gland attachment
    The spot where there power wires comes in requires a cable gland. Added a flat spot for the cable gland to mount to.
    [OpenLidarGimbal.f3d]
2021-08-03 Fixed Flat for Cable Gland
    [GimbalBaseMiddle.stl, OpenLidarGimbal.f3d]
